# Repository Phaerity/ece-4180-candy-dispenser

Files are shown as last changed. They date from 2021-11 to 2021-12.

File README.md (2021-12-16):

# 🍭Automated Candy Dispenser🍬 (ECE 4180 Fall 2021)
Made by: Ikenna Nwokedi, Harneet Sethi, Felicia E, Anna Yue

## 🍫Project Description🍫
This device dispenses candy in a hands-free manner, similar to how hands-free soap dispensers work. The dispenser will use a lidar to detect motion and a DC motor to spin some blades that release candy. Inside the dispenser, there is a sonar to detect how much candy is left, and this information is displayed as a status bar using colored LEDs. The dispenser itself will sit on a robot chassis such that someone can drive it around using Bluetooth.  

See the automated candy dispenser in action! - https://youtu.be/Ra_htNfpPXM

## ⚡Parts List⚡
### Robot Chassis
Dual H-bridge (https://www.sparkfun.com/products/14450)  
2 DC motors (https://www.sparkfun.com/products/13302)  
Chassis parts from kit (Sparkfun Shadow Chassis https://www.sparkfun.com/products/13301)  
Bluetooth module (https://www.adafruit.com/product/2479)  
Adafruit app on Andriod/iOS (Bluefruit Connect)  
Battery pack (comes with Shadow Chassis)  
Mbed (https://www.sparkfun.com/products/9564)  
### Candy Dispenser
Lidar (https://www.adafruit.com/product/3317)  
Sonar (https://www.sparkfun.com/products/15569)  
LEDs (1 red, 1 green, 1 yellow) (https://www.sparkfun.com/products/12062)  
Transistor (https://www.sparkfun.com/products/12959)  
1 DC motor (same as above)  
Plywood/MDF (https://www.homedepot.com/p/1-4-in-x-2-ft-x-4-ft-Medium-Density-Fiberboard-1508104/202089069#overlay)  
2 Battery packs (same as above, or https://www.sparkfun.com/products/9835)  
Mbed (same as above)  
Speaker (https://www.sparkfun.com/products/11089)  
Class D amplifier (https://www.sparkfun.com/products/11044)  
RGB LED (https://www.sparkfun.com/products/10820)  
uLCD (https://www.sparkfun.com/products/11377)  

### Miscellaneous
Wires  
Candy (about the size of Hershey Kisses)  
Wood glue  
Super glue  
Electrical tape  
Masking tape  
AA batteries (or 5V wall plugs)

## 🛠️Tools Needed🛠️
Laser cutter  
3D Printer  
Drill  

# How It Works
## Sonar and Capacity Indicator LEDs
One component of the project is a sonar and led system that continuously measures the depth of candies in the dispenser and alerts the user to how full the box currently is by turning on separate LEDs.  

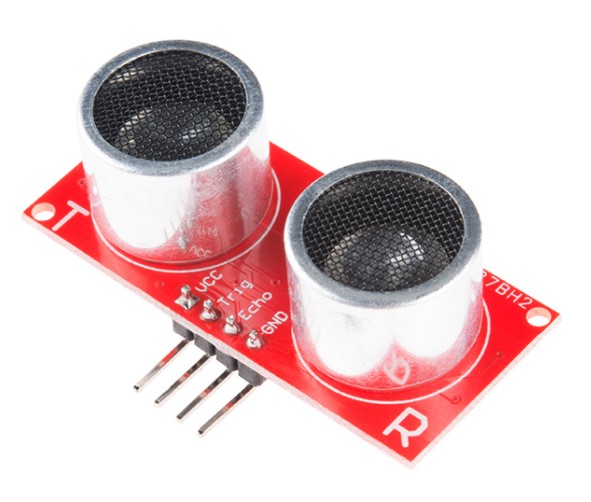
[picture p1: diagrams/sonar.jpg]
 
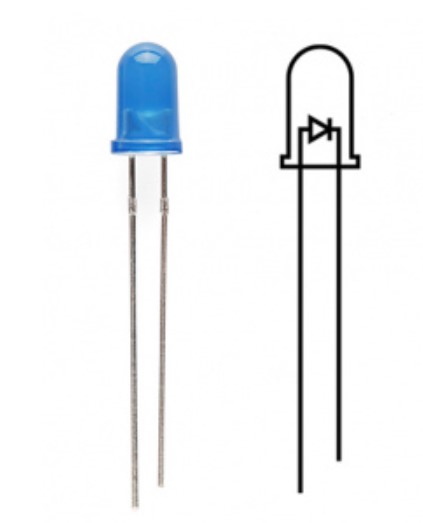
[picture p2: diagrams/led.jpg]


There are three LEDs: green to indicate a full box or a high level of candies, yellow to indicate a medium level of candies, and red to indicate a low level of candies that will need to be quickly replenished.

The sonar used is a HC-SR04 sonar module. It is mounted to the inside of the top of the box. The detection range is around3-400 cm with around a 15 degree beam width. Its transducers for transmitting and receiving signals are connected to the mbed microcontroller at pins 6 and 7. It uses its transducers to send out a signal and receive an echo back. The speed of sound and the time as returned by a timer interrupt for the delay transmission and reception are used to calculate the distance between the sonar and the candies closest to it.

Depending on the distance that the sonar measures, either one of the LEDs will be switched on while the others are turned off or all LEDs will be turned off and an error message will output through the COM port.  

## Lidar and DC Motor
Another component of the project is a lidar and DC motor system that performs the hand-motion detection and actual dispensing of the candy.  

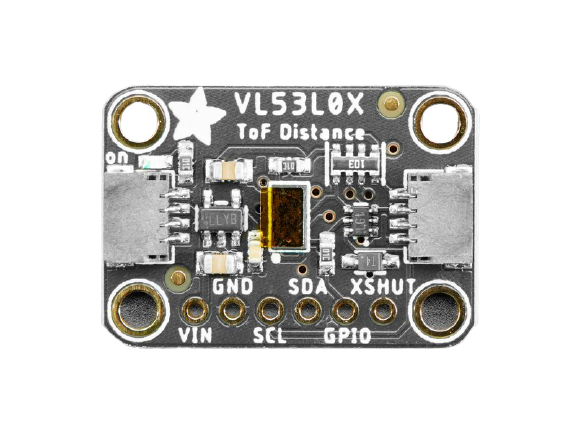
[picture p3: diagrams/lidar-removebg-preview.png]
 
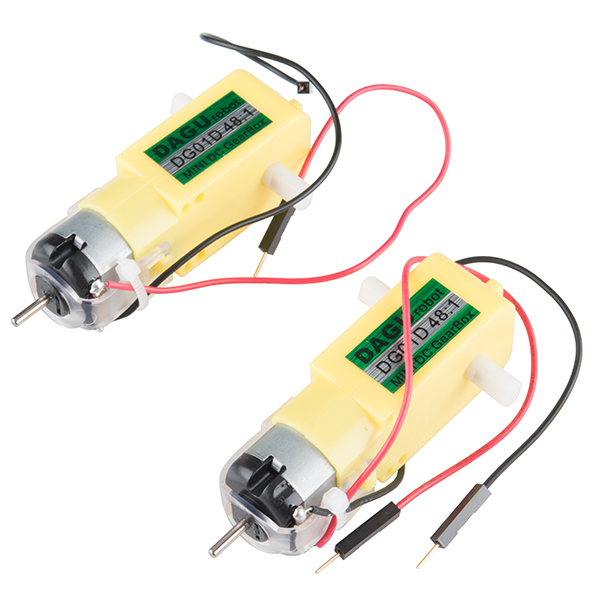
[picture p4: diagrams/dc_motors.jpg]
 

By reaching into the box with your hand open, the lidar is activated and the DC Motor will spin half a revolution, pushing out some candy with the attached 3D-printed blades.  

The lidar used is the VL53L0X module. It is able to detect distances from 30-1000 mm and works similarily to a sonar, except with light instead of ultrasonic waves and a smaller "cone" of detection.  

We specifically chose a lidar for this task due to the precision and reliability of the lidar measurements as well as its small size. Additionally, the lidar is situated pointing downwards so that it is always reading ~80 mm, so as soon as that reading drops to 65 mm it knows that some motion is being detected.  

The DC Motor is a standard motor that can be exchanged for a servo if desired. We primarily chose the DC Motor because the axle was easy to design a part to fit onto.  

## uLCD, Speaker, and RGB led
The last component of the candy dispenser itself includes the uLCD, speaker, and RGB led.  







Each of these devices alerts the user if their hand has been detected by changing state. At initialization and when no hand is detected, the uLCD provides instructions for how to use the automated dispenser, the RGB led is off, and the speaker is not playing any sounds. Upon a hand-motion detection, the lidar triggers the uLCD to display instructions on how to stop receiving candy, the RGB led is lit up white, and the speaker plays Ramblin' Wreck. This state is present until the hand is no longer detected.

The RGB led is placed on top of the dispenser for an easy visual indicator of whether a user's hand has been detected by the dispenser. The color of the RGB can be changed at any time in software, since the pin connections used support PWM. For the purposes of the prototype, white was used.

The speaker is attached to a breadboard which is mounted to the top of the inside of the dispenser. This design decision allows the dispenser to be more visually appealing, by concealing the speaker, but also provides an auditory indicator associated with the lidar detecting a hand motion. In some instances (depending on the sound/tone being played), the speaker needs to be driven for better audio quality. Therefore, this project includes a Class D Audio Amplifier (TPA2005D1) attached to the breadboard and wired to the speaker (pin connections included below). This approach uses PWM hardware which is more energy efficient than using analog. The SongPlayer header file is used in software, which means the song/sound and the volume can be easily changed/adjusted at anytime by modifying the appropriate parameters.

Lastly, the uLCD is mounted to the front of the dispenser so that the instructions can be viewed at all times by the users, even while the dispenser is moving on the chassis. The text, formatting, etc. on the uLCD can all be altered depending on the circumstance of when the dispenser is being used. The associated uLCD header file makes changing the settings of the uLCD very manageable. 

## Robot Chassis
The robot chassis consists of two DC motors, a dual TB6612FNG H-Bridge and an Adafruit Bluefruit LE UART Friend board.

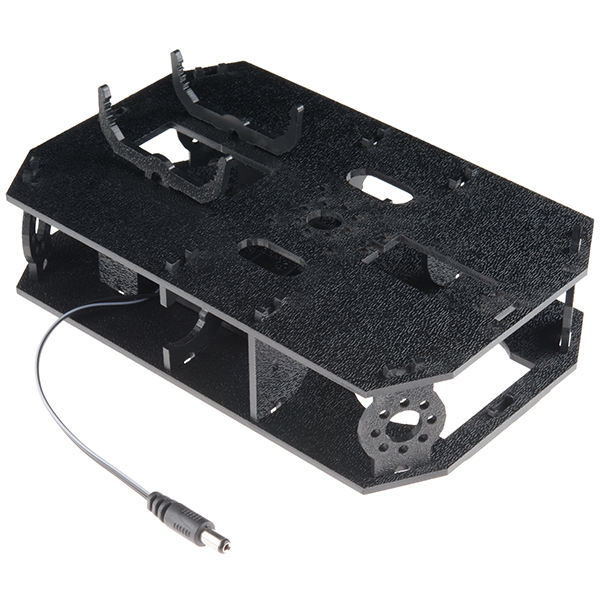
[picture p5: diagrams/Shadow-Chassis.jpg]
Shadow-Chassis

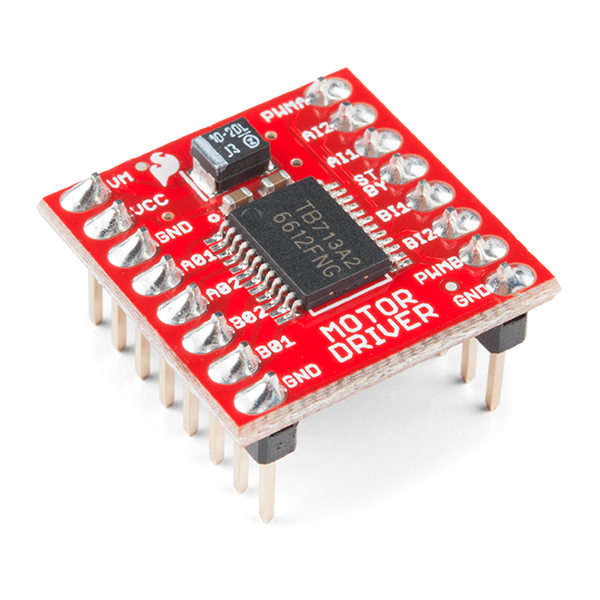
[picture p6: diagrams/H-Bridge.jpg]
H-Bridge

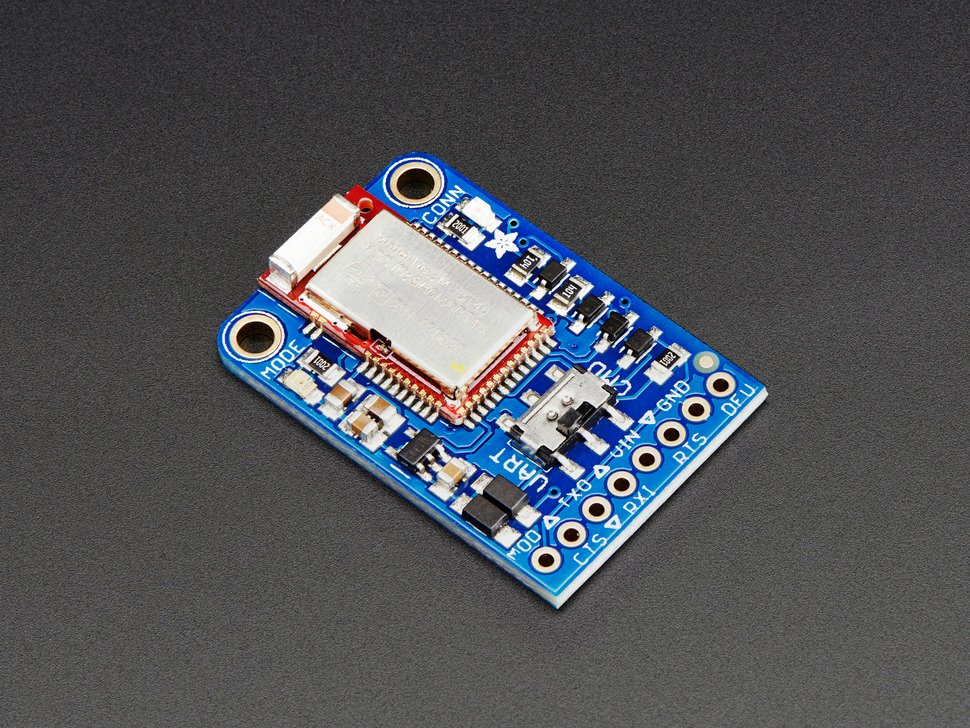
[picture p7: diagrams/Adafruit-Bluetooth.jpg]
Adafruit-Bluetooth


Using the Adafruit Bluefruit BLE app, buttons 1, 2, 3, and 4 are used to set the speed level of the wheels (on a scale from 0 to 1). While the up and down buttons move the motors forward and backward respectfully, the left and right buttons inverse the direction of both motors, resulting in a rotational movement around the chassis center. The motors gradually increase to their set speed for a duration of a second to keep the mbed from undervolting. This is done with a separate thread that starts once a directional button is pressed then terminates at the release of the button. Upon press of a button, an ASCII string is sent to the bluetooth board, which is then decoded in the mbed. More details can be found below.

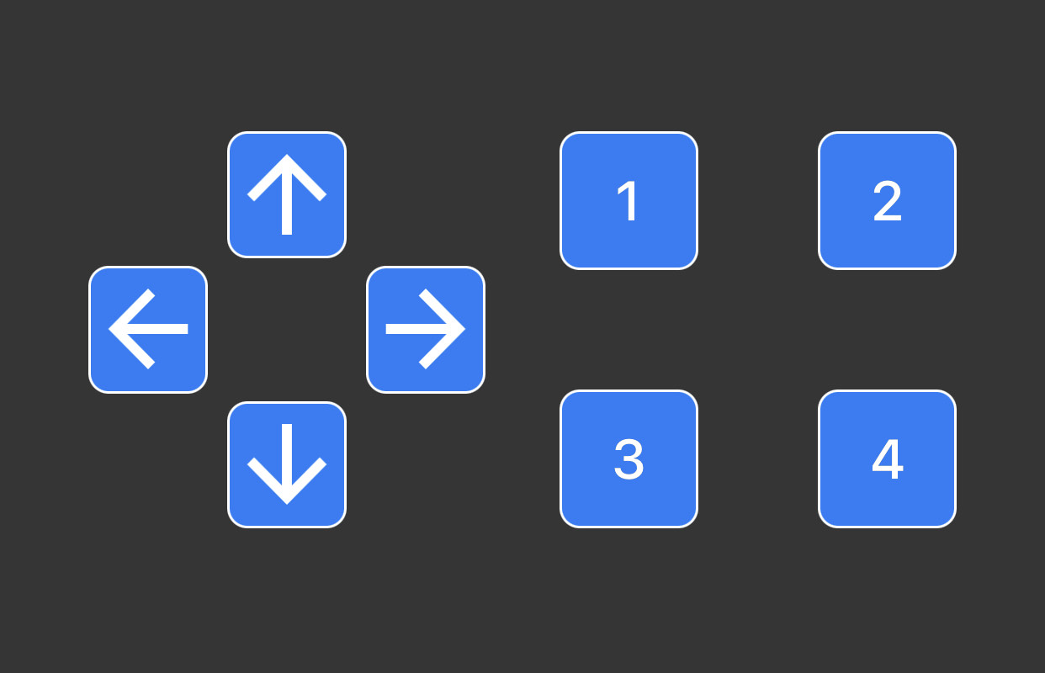
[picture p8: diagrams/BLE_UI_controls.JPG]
UI Controls


| GUI Touch Key  | ASCII String | Motor Function
|:---: |:---:|:---:|
| Button 1  | "!B11" | 0.25 of max speed |
| Button 2  | "!B21" | 0.50 of max speed |
| Button 3  | "!B31" | 0.75 of max speed |
| Button 4 | "!B41" | Max speed |
| Up Arrow  | "!B51" | Moves forward |
| Down Arrow  | "!B61" | Moves backwards |
| Left Arrow  | "!B71" | Turns left |
| Right Arrow  | "!B81" | Turns right |

# Instructions
## Cutting the Box
We started off by creating box using the website https://en.makercase.com/#/. The settings we used are as follows: Basic Box, Width 5 in., Height 8 in., Length 8 in., Outside dimensions, Material Thickness 1/4 in., Closed box, Finger joints sized 1.0915. These settings can be customized based on how big you want the dispenser to be and thickness of your wood. The box plans can be downloaded with labels disabled and separate panel layout, and these files can be used to laser cut the box at either the Hive or Invention Studio. The files we used (with Inkscape) are provided in the diagrams folder (box.svg).

> **Note:** For our project, we used 1/4" MDF to create the box, but we realize that lighter wood is preferable to reduce the weight of the dispenser. Therefore, you may want to consider using birch plywood or balsa wood.  

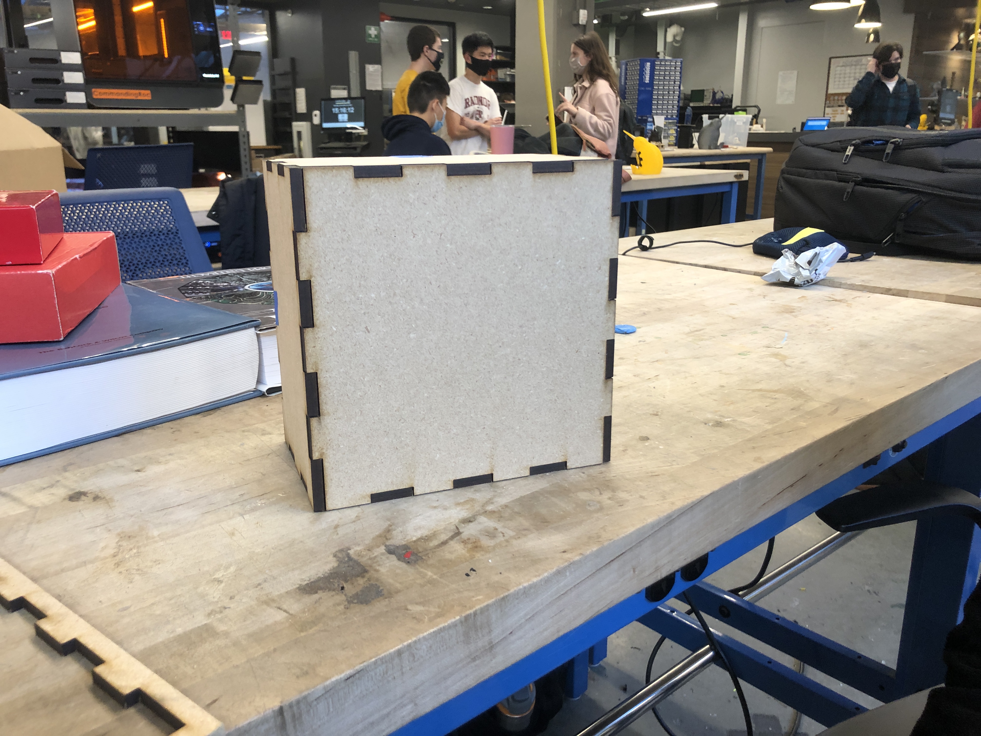
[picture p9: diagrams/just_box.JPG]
Laser Cut Box


Furthermore, the box must be modified so that the bottom panel becomes like a shelf (see picture). We cut rectangular holes into the sides of the box so that the shelf could "slide" in, but there are other ways to do it if preferable.  

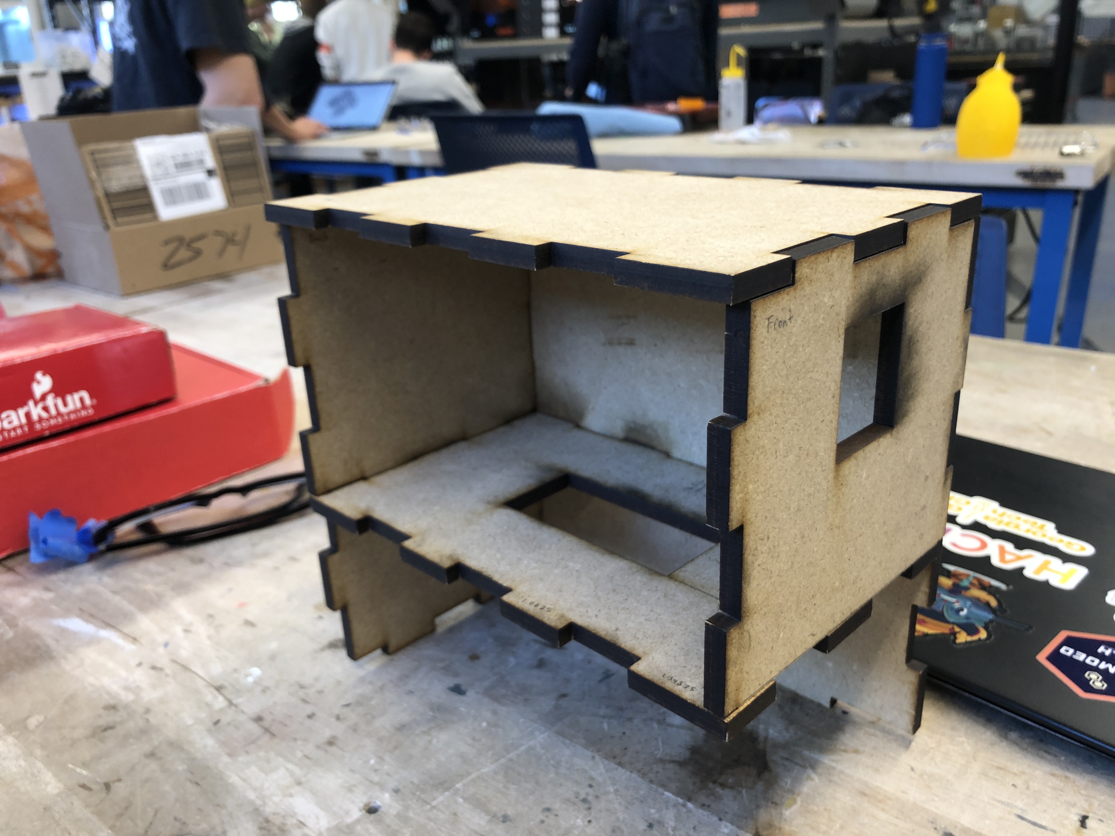
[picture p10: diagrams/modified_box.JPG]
Modified Box


An additional rectangular hole was cut on the back panel to facillitate wiring, but again this can be changed as you see fit.  
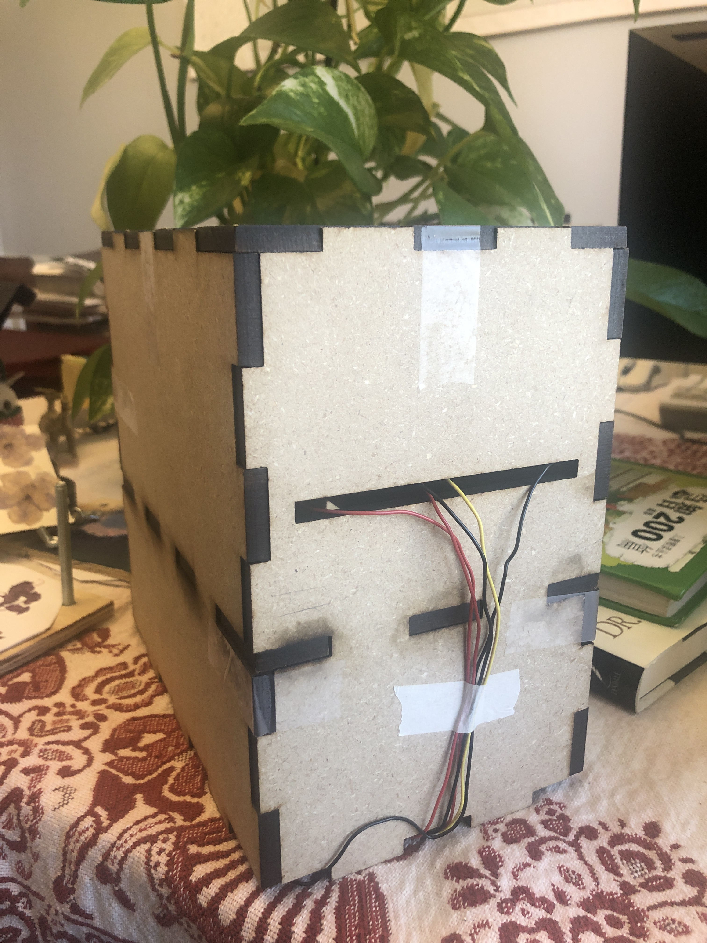
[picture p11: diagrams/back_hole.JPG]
Wire Hole Wiring hole
  

For the LED holes, we used a 7/32" drill bit and approximated the locations. The red, yellow, and green LEDs are on the front panel, and the RGB LED is on the top panel. For the uLCD hole, we cut a 32mm (width) by 38mm (length) rectangle on the front panel. For the windmill blade hole, we cut a 40mm (width) by 80mm (length) rectangle on the shelf panel.  

> **Note:** We originally proposed using an LED array to display the status for the amount of candy left, but we changed this to individual LEDs to avoid having to replace the parts at the end of the semester.

## The Blades
For the part that releases the candy (referred to as windmill blades), we created a CAD model to 3D print. We used Autodesk Inventor to draw the model before exporting it as an stl file and transferring it to 3D printer software. These files can be found in the diagrams folder (windmillv3.stl and windmillv3.ipt). Our windmill blades are made from PLA.  

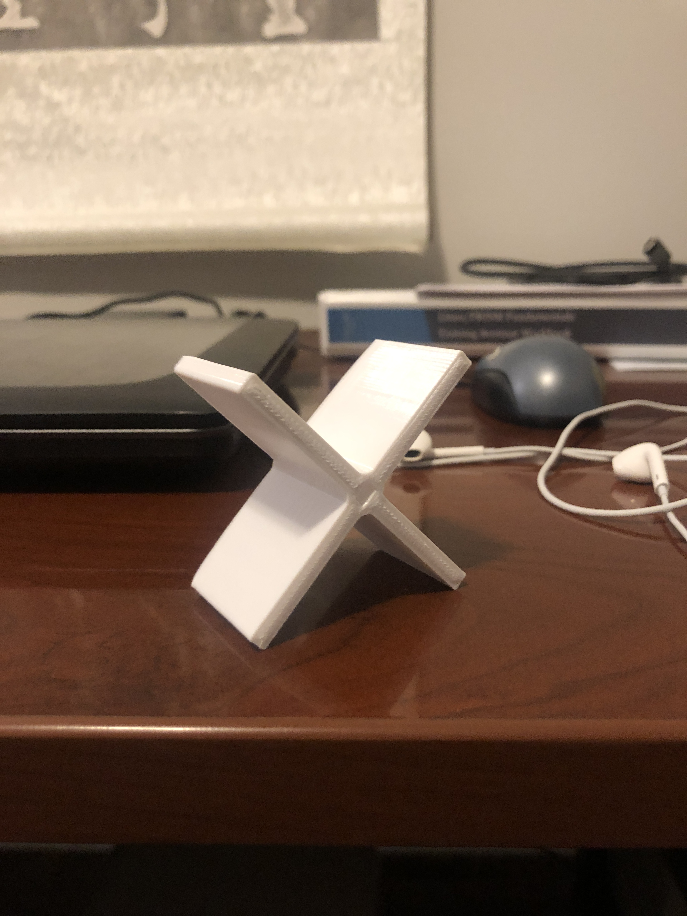
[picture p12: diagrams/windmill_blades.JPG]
Windmill Blades


## Assembling the Box
Once the box is cut with all the correct holes and the windmill blades are printed, we can start mounting components in the box. For the purposes of our prototype, components were either taped or glued down, but screws/standoffs are needed if a more permanent solution is desired.  

The uLCD can be first installed by pushing it into the rectangular hole in the front panel. There is a base on the uLCD that prevents it from going all the way through the hole. The windmill blades should snap onto the DC motor axle, and the motor should be positioned on the shelf panel so that the blades can spin freely through the rectangular hole in the shelf panel.  
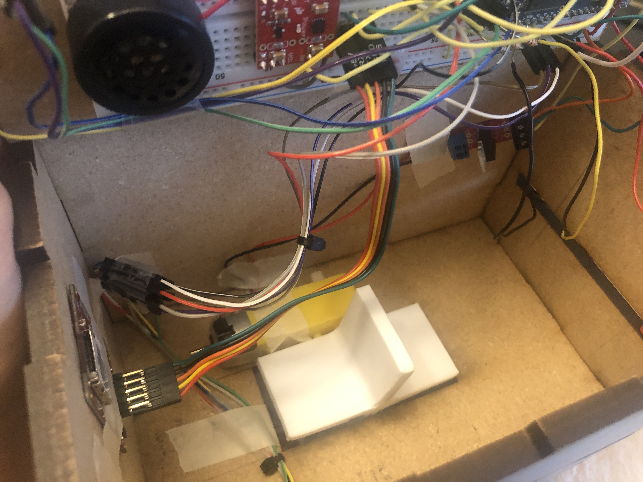
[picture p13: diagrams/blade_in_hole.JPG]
DC motor and blades DC motor and windmill blades
  
The sonar is attached to the underside of the top panel, such that it has a clear vision of the shelf panel without interference from the motor or blades.  
Under the lid Sonar, speaker, mbed under the lid  
The LEDs can be pushed through their respective holes and also have a base that prevent them from going all the way through the hole. The lidar is situated on a small breadboard that is attached to the underside of the shelf panel closest to the side where someone would stick their hand through.  

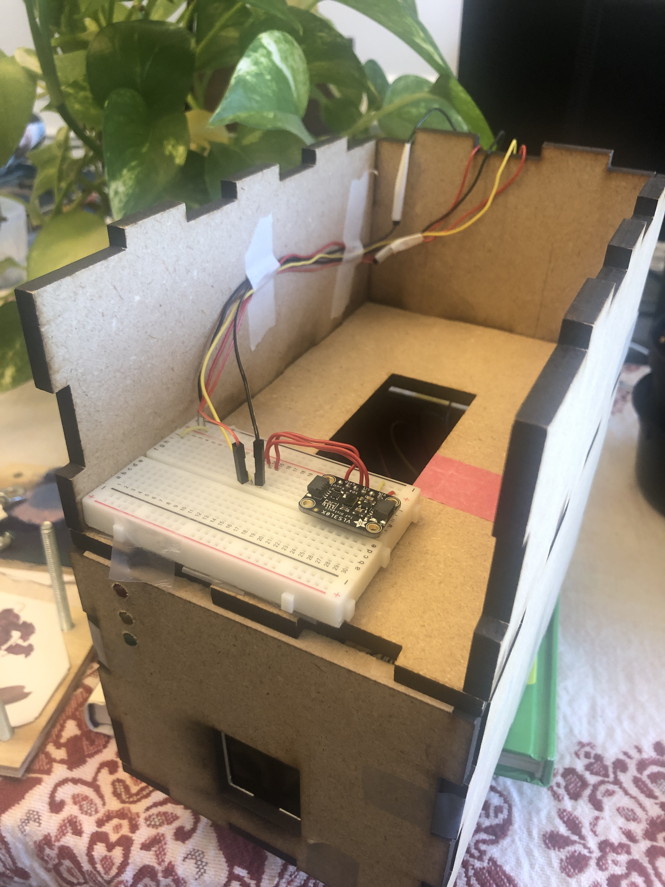
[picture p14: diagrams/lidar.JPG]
Lidar Lidar underneath
  

Once the components are in place, they can be wired following the schematics/tables below. 

Schematic 1

<table>
<tr><th> Sonar </th><th>LED </th></tr>
<tr><td>

| mbed | HC-SR04 |
| :----: |:----:|
| GND  | GND |
| VU (5V) | VCC |
| P6 | TRIG |
| P7 | ECHO |

</td><td>

| mbed | LEDs |
| :---: |:---:|
| GND  | RED(-), YELLOW (-), GREEN (-) |
| P12  | Red (+) |
| P13 | YELLOW (+) |
| P14 | GREEN (+)|
  
</td></tr> </table>

<table>
<tr><th> MOSFET </th><th> DC Motor </th></tr>
<tr><td>

| mbed | MOSFET (Transistor)|
| :---: |:---:|
| VU (5V) | GND (JP2-2 GND) |
| GND  | POWER (JP2-1 RAW) |
| P8  | CONTROL |

 </td><td>

| MOSFET (Transistor) | DC Motor |
| :---: |:---:|
| GND (JP1-2) | GND (-) |
| POWER (JP1-1) | POWER (+) |

</td></tr> </table>

<table>
<tr><th> Lidar </th><th> uLCD </th></tr>
<tr><td>

| mbed  | LIDAR (VL53L0X) |
| :---: |:---:|
| VOUT (3.3V) | VIN |
| VU (5V) | VCC |
| GND  | GND |
| P25  | SHDN |
| P27  | SCL |
| P28  | SDA |

</td><td>

| mbed  | uLCD HEADER | uLCD CABLE |
| :---: |:---:|:---:|
| GND  | GND | GND |
| VU (5V)  | 5V | 5V |
| P9 | RX | TX |
| P10 | TX | RX |
| P11 | RESET | RESET |

</td></tr> </table>

<table>
<tr><th> RGB LED connections </th><th>Speaker connections</th></tr>
<tr><td>

| mbed  | RGB LED |
| :---: |:---:|
| GND  | GND |
| P21  | RED |
| P22  | GREEN |
| P23  | BLUE |

</td><td>

| mbed  | Amp (TPA2005D1) | Speaker |
| :---: |:---:|:---:|
| GND  | PWR- (GND), IN- |
| VU (5V)  | PWR+ |
| P26  | IN+ |
| | OUT+ | + |
| | OUT- | - |

</td></tr> </table>

## The Chassis
The robot chassis can be assembled following the Sparkfun guide: https://learn.sparkfun.com/tutorials/assembly-guide-for-redbot-with-shadow-chassis. Bluetooth control is added using the Adafruit Bluefruit LE UART Friend board. The Adafruit board mini slide must be set to "UART" (not "CMD"). The "Adafruit Bluefruit BLE" app is used for the user interface and can be found on iOS and Andriod. Select "UART" mode on the phone window and connect to the board. A blue LED should turn on once connected.

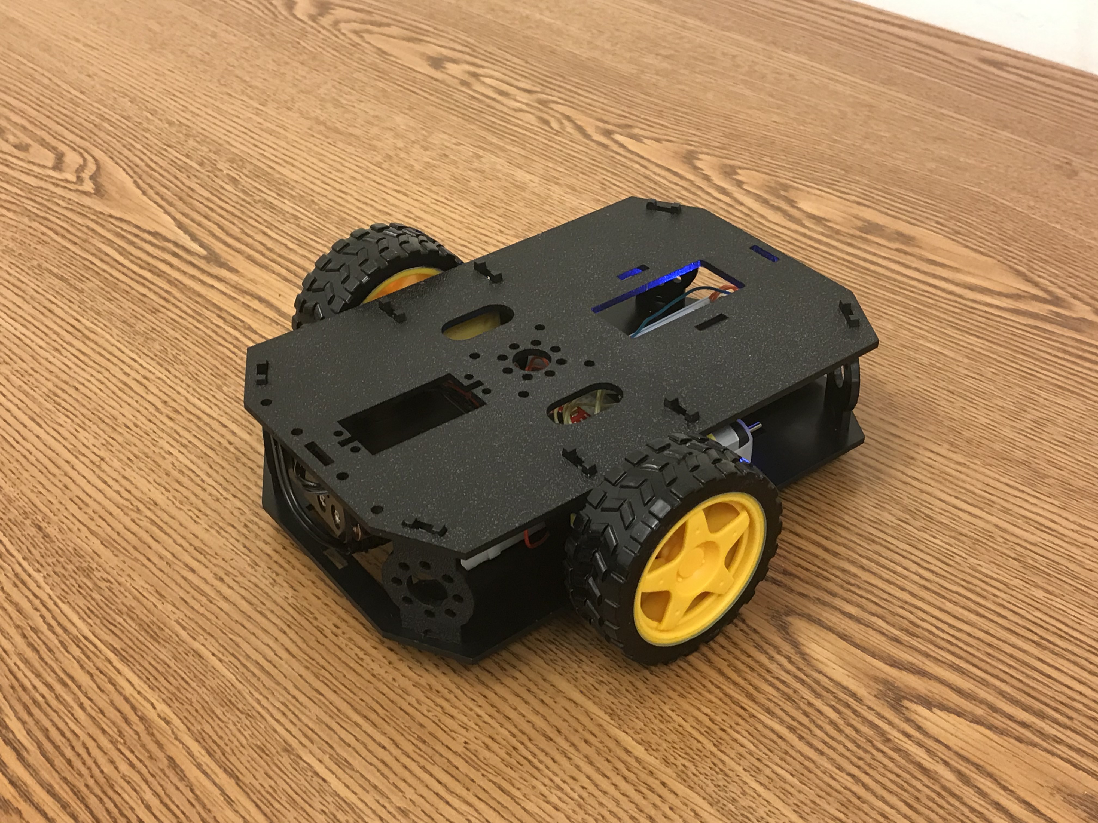
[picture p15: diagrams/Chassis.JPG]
Chassis

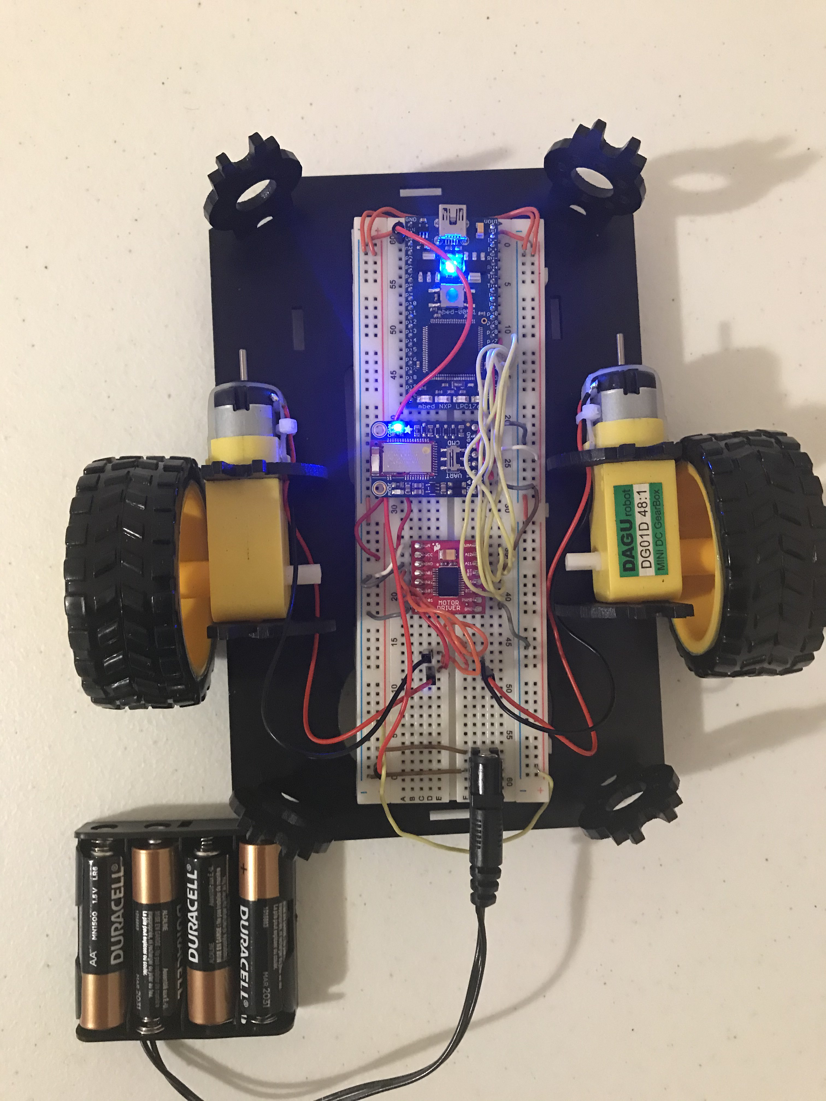
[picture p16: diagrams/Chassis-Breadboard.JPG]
Chassis Breadboard


A 6 V battery pack is used to power the two motors attached to the wheels. A dual H-bridge will regulate the speed and direction of the motor wheels. Both the breadboard implementation and the battery pack will fit into the robot chassis. The schematics/tables for the integration can be found below. 

Schematic 2

<table>
<tr><th> Bluetooth </th><th> H-Bridge </th><th> Motor </tr>
<tr><td>

| mbed | Adafruit BLE  |
| --- |:---:|
| VU (5V) | Vin (3.3-16V) |
| P27 (RX) | TXO |
| P28 (RX) | RXI |
| GND | GND |
| NC | RTS |

</td><td>

| mbed | H-Bridge |
| --- |:---:|
| P21 | PWMA |
| P22 | AIN1 |
| P23 | AIN2 |
| P24 | PWMB |
| P25 | BIN1 |
| P26 | BIN2 |
| VOUT | STBY |
| GND | GND |

</td><td>

| H-Bridge | Battery Pack | Left Motor | Right Motor |
|:---:|:---:|:---:|:---:|
|GND|GND  ||
|VM, VCC|5V|||
|A01||GND (BLACK)||
|A02||POWER (RED)||
|B01|||POWER(RED)|
|B02|||GND(BLACK)|

</td></tr> </table>

## Combining Everything
We found that the components for the dispenser drew too much current for one battery pack to handle, so we use two battery packs for the dispenser. Specifically, the DC motor is powered by one battery pack, and everything else is powered by the other battery pack. One battery pack sits on top of lid and one is located below shelf, sitting on top of chassis. 

The lidar, DC Motor, RBG LED, uLCD, speaker, sonar, and capacity LEDS are all controlled by a mbed microcontroller running multi-threaded RTOS code mounted on the inside of the top wooden pane. All devices except the DC motor and lidar are powered by one 5 V battery pack. The lidar uses 3.3 V output from the mbed micro controller and the DC motor has a separate battery pack for power, as mentioned before. Both battery packs are connected to two external power source connection jacks on a breadboard mounted on the back of the box. 

The dispenser box itself sits exactly on the top of the chassis. The chassis itself is controlled by a separate mbed microcontroller.

All code, for the dispenser devices as well as the robot chassis, can be found in the finalCode folder on this github page (chassis.cpp and the Motor folder are for the chassis mbed, main.cpp and everything else are for the dispenser mbed).   

## Conclusion

The completed candy dispenser robot is able to move forward, backward, left, and right as directed by the user's Bluefruit Connect application. The candy dispenser is able to drive up to a person and instruct them to "Place hand under dispenser to receive candy" in red text. Once the LIDAR sensor detect an object/the user's hand, it will trigger four events: a song will play from the speaker for as long as the user's hand is underneath the lidar, the uLCD's text will turn green to indicate the user's hand has been sensed, the RGB LED will flash on to indicate dispensing in progress, and the DC motor will turn to release a candy. The entire time, the sonar will be constantly measuring the depth of candy in the box; turning on the green, yellow, and red LEDs respectively when the candy volume is high, medium, or low.

giphy

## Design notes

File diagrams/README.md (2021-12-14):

# Diagrams/Pictures

🖼️🖼️🖼️

Schematic 1

Schematic 2

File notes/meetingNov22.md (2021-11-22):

# In-Person Meeting 11/22/21
Members present: Harneet, Felicia, Ikenna, Anna

# Notes
## Diagramming robot
We drew out how the robot looks in full, including all parts and where they will be in relation to the robot:
Whiteboard drawings  
Felicia diagrammed a 3D version of the robot in Paint 3D

### There will be 3 "levels" built out of wood:
1. Bottom level houses the mbed, motors, and bluetooth for the robot chassis
2. Middle level is open for a hand to insert into - like a square with 3 sides
3. Top level is the actual dispenser, with the candy
### Changing LED array to individual for fullness status
To avoid having to take it apart at the end of the semester - **add to the report** since changed from the original design
### Structure to dispense the candy is similar to a windmill, turns 90 degrees to dispense
There will be a rectangular hole at the bottom of the actual dispenser
### Inside the actual dispenser, we can install slanted boards to help with candy not getting stuck at the corners (OPTIONAL)
### The mbed and speaker for the actual dispenser will be mounted on the back, exposed
### The sonar will be on the ceiling of the dispenser
### The lid will be separate from the box
Will need to be detachable - hinge, velcro, tape, etc.

# TODO
Port to github.com, github.gatech.edu will require logon for the grader  
Finish wood stuff by Dec. 3 - Invention Studio will close by then so no laser cutter

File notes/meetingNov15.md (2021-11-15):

# 11/15/21 Virtual Meeting

Members present: Ikenna, Felicia, Harneet, Anna

## Splitting project into 4 parts
1. Motion sensing + opening/closing latch (lidar + servo) - Anna
    - Ikenna has motion sensing code for arduino from previous project
2. Robot chassis + bluetooth (bluefruit app) to drive + power (on its own mbed) - Ikenna
3. Sonar + LED array (status for fullness) + building the box - Felicia
4. LEDs (+ LCD maybe) for decoration (open for interpretation) + speaker/sound + power (battery pack) - Harneet

All help with robot if needed  
Next meeting draw out how it all looks together (esp. box)

## Requirements:
Documentation on the project web page must include team member names, a parts list, schematic, source code, photos, and videos.  

The web page should explain the project idea, provide instructions, code, and hardware setups so that anyone could recreate your project along with photos and videos along with team member names. It might make sense to have a longer video on the web page 

### Ask Dr. Hamblen:
Show what we have, see if it's what he meant (Github documentation)  
Is github.gatech.edu okay?  
Lab still open?

### Other notes:
Maybe don't use LED array because will have to return it - uLCD instead of this? ask Oscar or Maddie

## Schedule:
Nov. 22 - meeting to draw out how it all looks/interacts together (Hive 12:30, whiteboard)  
Nov. 22-30 - Work on individual parts, help others if needed  
Nov. 29 - class time to make sure all individual parts are working  
Dec. 1 & 6 - class time to put everything together  
Dec. 1-10 - Integration  
Dec. 11-14 - Finalize documentation and presentation  
Dec. 15 - presentation day  
  
How to format this page: https://docs.github.com/en/github/writing-on-github/getting-started-with-writing-and-formatting-on-github/basic-writing-and-formatting-syntax

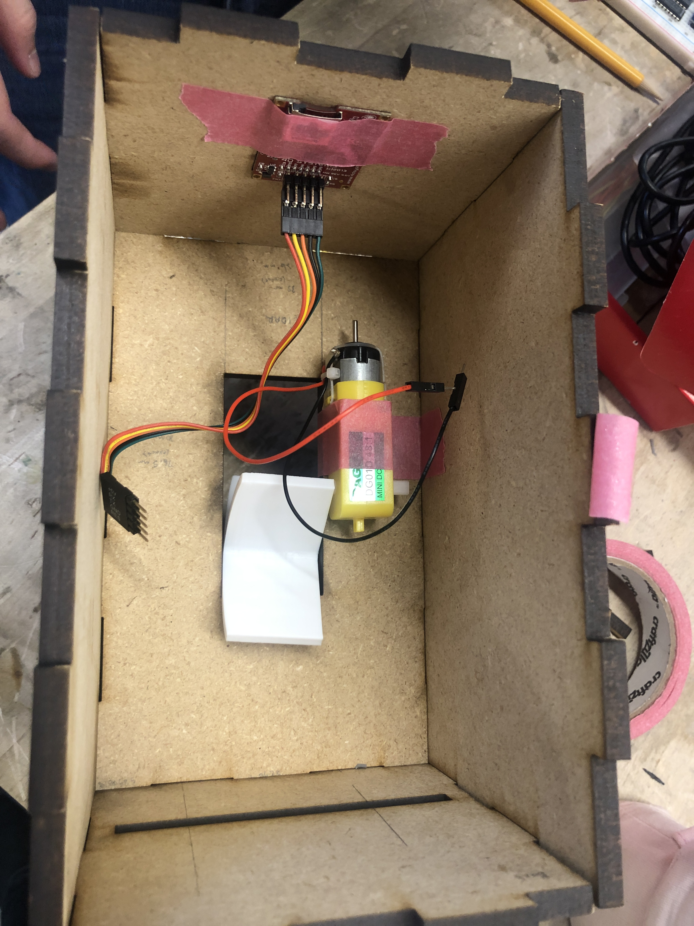
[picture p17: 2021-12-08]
diagrams/mount_lcd.JPG

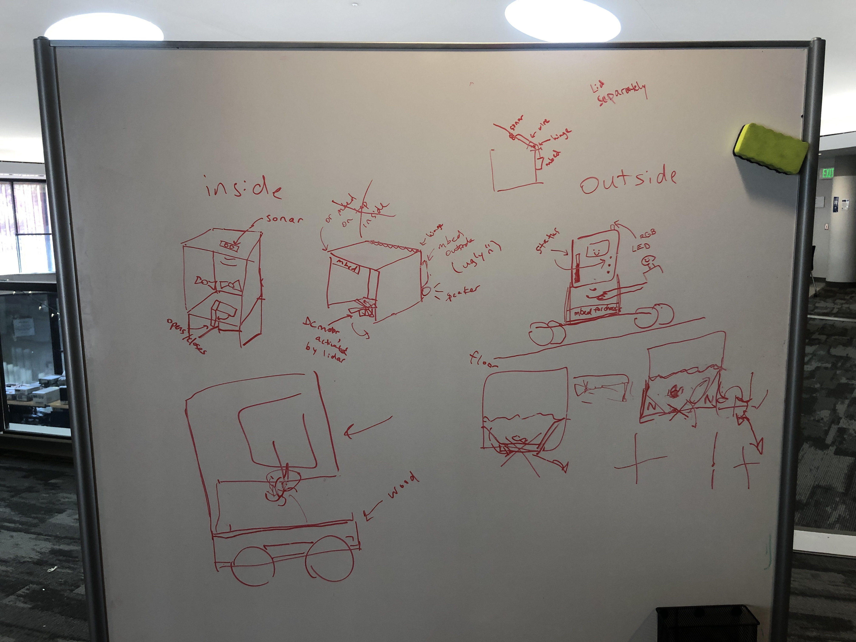
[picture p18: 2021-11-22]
diagrams/whiteboardNotes.JPG

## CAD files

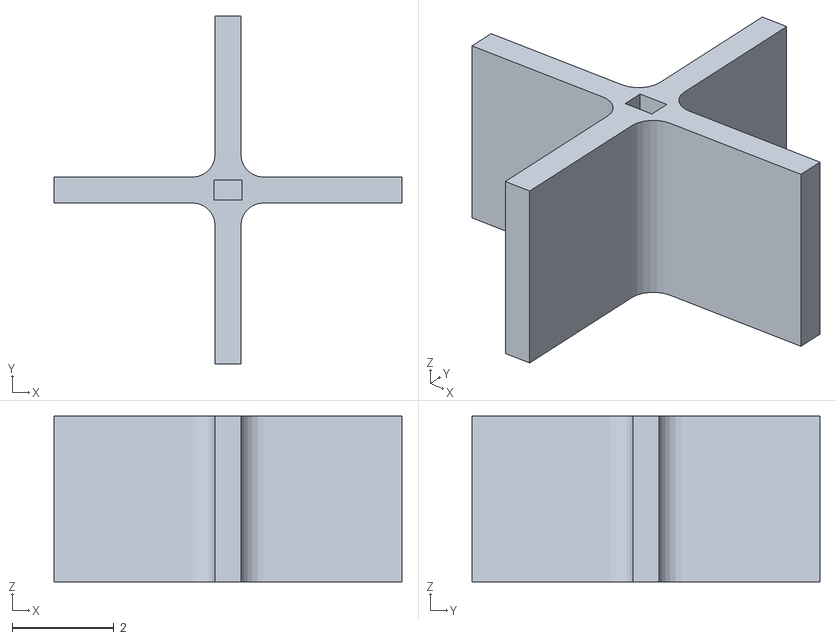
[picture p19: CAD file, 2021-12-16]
diagrams/windmillv3.stl
6.83 x 6.83 x 3.25

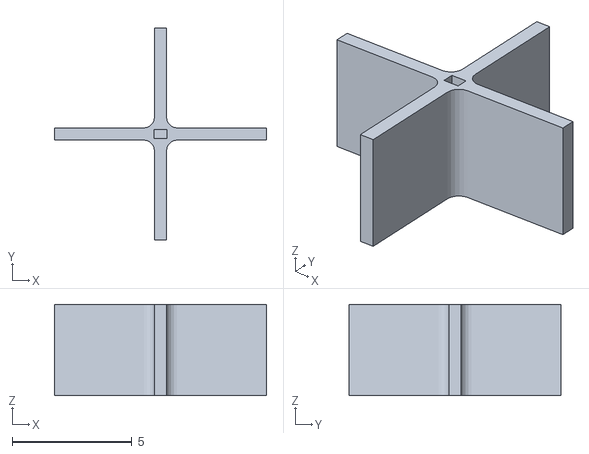
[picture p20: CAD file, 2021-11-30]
diagrams/windmillv2.stl
8.87 x 8.87 x 3.81

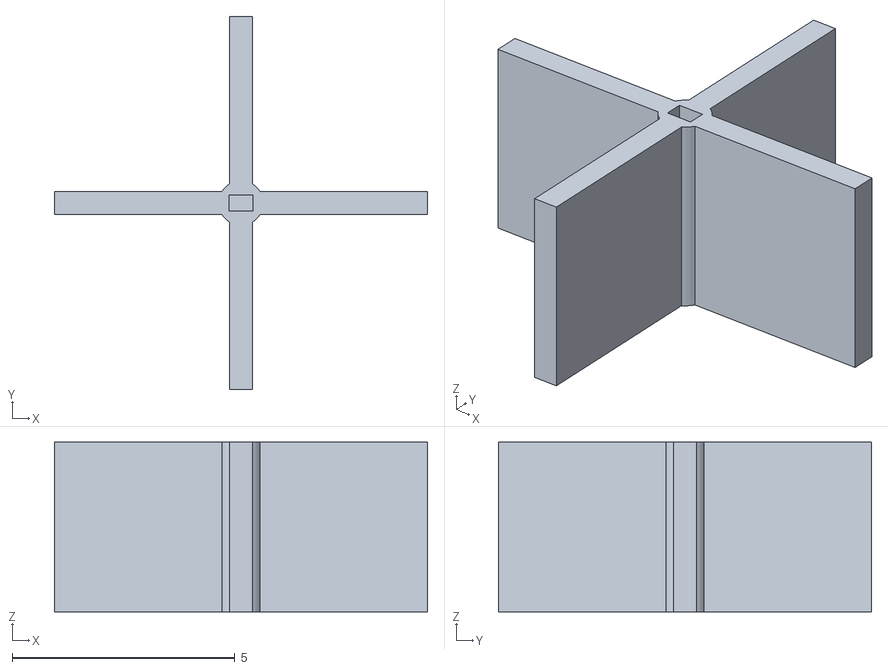
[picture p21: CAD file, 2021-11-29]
diagrams/windmill.stl
8.37 x 8.37 x 3.81

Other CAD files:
diagrams/windmill.ipt
diagrams/windmillv2.ipt
diagrams/windmillv3.ipt

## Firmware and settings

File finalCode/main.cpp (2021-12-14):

/*
 * Main code for automated candy dispenser.
 *
 * Adapted from RTOS, lidar, and sonar hello world code.
 */

#include "mbed.h"
#include "rtos.h"
#include "XNucleo53L0A1.h"
#include <stdio.h>
#include "uLCD_4DGL.h"
#include "SongPlayer.h"

Serial pc(USBTX,USBRX);
uLCD_4DGL uLCD(p9,p10,p11); // serial tx, serial rx, reset pin;

//Set up notes and durations for sample song to play
// A 0.0 duration note at end terminates song play
float note[18]= {1568.0,1396.9,1244.5,1244.5,1396.9,1568.0,1568.0,1568.0,1396.9,
                 1244.5,1396.9,1568.0,1396.9,1244.5,1174.7,1244.5,1244.5, 0.0
                };
float duration[18]= {0.48,0.24,0.72,0.48,0.24,0.48,0.24,0.24,0.24,
                     0.24,0.24,0.24,0.24,0.48,0.24,0.48,0.48, 0.0
                    };

// For the sonar
DigitalOut trigger(p6);
DigitalIn  echo(p7);

float distance = 0;
float correction = 0;
Timer sonar;
DigitalOut red(p12);
DigitalOut yellow(p13);
DigitalOut green(p14);

// For the lidar
DigitalOut RGBred(p21);
DigitalOut RGBgreen(p22);
DigitalOut RGBblue(p23);

SongPlayer mySpeaker(p26);
volatile bool changed = false;

DigitalOut shdn(p25);
 
DigitalOut myled(LED1); // comment out later
PwmOut Ctrl(p24);
// This VL53L0X board test application performs a range measurement in polling mode
// Use 3.3(Vout) for Vin, p28 for SDA, p27 for SCL, P26 for shdn on mbed LPC1768

//I2C sensor pins
#define VL53L0_I2C_SDA   p28
#define VL53L0_I2C_SCL   p27

static XNucleo53L0A1 *board=NULL;

// Callback routine is interrupt activated by lidar
/*void pb_hit_callback (void) {

    //mySpeaker = 0.5;
    mySpeaker.PlaySong(note, duration, 0.1);
    RGBred = 1;
    RGBgreen = 1;
    RGBblue = 1;
    //Put uLCD stuff here
    uLCD.cls();
    uLCD.color(GREEN);
    //uLCD.locate(2,1);
    uLCD.printf("Remove hand to stop receiving candy\n");
    changed = true;
}*/

// Thread 1
// sonar detection
void thread1(void const *args)
{
    sonar.reset();
    // measure actual software polling timer delays
    // delay used later in time correction
    // start timer
    sonar.start();
    // min software polling delay to read echo pin
    while (echo==2) {};
    // stop timer
    sonar.stop();
    // read timer
    correction = sonar.read_us();
    pc.printf("Approximate software overhead timer delay is %f uS\n\r", correction);

    //Loop to read Sonar distance values, scale, and print
    while(1) {
    // trigger sonar to send a ping
        trigger = 1;
        sonar.reset();
        wait_us(5.0);
        trigger = 0;
    //wait for echo high
        while (echo==0) {};
    //echo high, so start timer
        sonar.start();
    //wait for echo low
        while (echo==1) {};
    //stop timer and read value
        sonar.stop();
    //subtract software overhead timer delay and scale to cm
        //printf("The time taken was %d seconds\n", sonar.read_us());
        ::distance = (sonar.read_us()-correction)/58.0;
        //pc.printf(" %f cm \n\r", ::distance);
        if (::distance <= 6.53) {
            green = 1;
            yellow = 0;
            red = 0;
            //pc.printf("GREEN \n\r");
        } else if ((::distance > 6.53) && (::distance <= 8.167)) {
            green = 0;
            yellow = 1;
            red = 0;
            //pc.printf("YELLOW \n\r");
        } else if ((::distance > 8.167) && (::distance <= 9.8)) {
            green = 0;
            yellow = 0;
            red = 1;
            //pc.printf("RED \n\r");
        } else if (::distance > 9.8) {
            green = 0;
            yellow = 0;
            red = 1;
            //pc.printf("ERROR: %f cm is larger than the box \n\r", ::distance);
        }
            
    //wait so that any echo(s) return before sending another ping
        Thread::wait(50);
    }
}

int main()
{
    int status;
    uint32_t distance;
    DevI2C *device_i2c = new DevI2C(VL53L0_I2C_SDA, VL53L0_I2C_SCL);
    /* creates the 53L0A1 expansion board singleton obj */
    board = XNucleo53L0A1::instance(device_i2c, A2, D8, D2);
    shdn = 0; //must reset sensor for an mbed reset to work
    wait(0.1);
    shdn = 1;
    wait(0.1);
    /* init the 53L0A1 board with default values */
    status = board->init_board();
    while (status) {
        pc.printf("Failed to init board! \r\n");
        status = board->init_board();
    }
    
    // Setup Interrupt callback function for a pb hit
    //pb.attach_deasserted(&pb_hit_callback);
    pc.printf("Initialized lidar\r\n");
    
    // Init ulcd
    uLCD.cls();
    uLCD.baudrate(3000000); //jack up baud rate to max
    uLCD.text_height(2);
    uLCD.text_width(2);
    uLCD.color(RED);
    uLCD.printf("Place hand under dispenser to receive candy!\n");
    changed = false;
    
    pc.printf("initizlized ulcd\r\n");
    
    // start threads
    Thread t1(thread1); //start thread1
    
    pc.printf("Starting main loop\r\n");
    //loop taking and printing distance
    while (1) {
        status = board->sensor_centre->get_distance(&distance);
        if (status == VL53L0X_ERROR_NONE) {
            //pc.printf("D=%ld mm\r\n", distance);
            RGBred = 0;
            RGBgreen = 0;
            RGBblue = 0;
            mySpeaker.PlaySong(note, duration, 0.0);
            if (changed) {
                uLCD.cls();
                uLCD.color(RED);
                uLCD.printf("Place hand under dispenser to receive candy!\n");
                changed = false;
            }
            
            if (distance < 70) {
                Ctrl = 0;
                for (int i = 0; i < 10; i++) {
                    Ctrl = Ctrl + 0.1;    
                }
                Thread::wait(80);
                for (int i = 0; i < 10; i++) {
                    Ctrl = Ctrl - 0.1;    
                }
                
                mySpeaker.PlaySong(note, duration, 0.01);
                RGBred = 1;
                RGBgreen = 1;
                RGBblue = 1;
                //Put uLCD stuff here
                uLCD.cls();
                uLCD.color(GREEN);
                uLCD.printf("Remove hand to stop receiving candy\n");
                changed = true;
                
                while (distance < 70) {
                    status = board->sensor_centre->get_distance(&distance);
                    Thread::wait(10);
                }
                //Thread::wait(4500);
            }
        }
        Thread::wait(10);
    }
}

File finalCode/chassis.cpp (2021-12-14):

#include "mbed.h"
#include "Motor.h"
#include "rtos.h"

Motor DC_Motor_Left(p21, p22, p23);
Motor DC_Motor_Right(p24, p25, p26);
Serial Blue(p28, p27);
Serial pc(USBTX, USBRX);
Thread MotorThread;

#define SPEED1 0.25f
#define SPEED2 0.50f
#define SPEED3 0.75f
#define SPEED4 1.0f

float curr_speed = SPEED1;
float left_speed = 0.0f;
float right_speed = 0.0f;
float direction = 1.0f;

void startMotors() {
    float inten = 0.0f;
    while (inten < 1.0f) {
        DC_Motor_Left.speed(inten * direction * left_speed);
        DC_Motor_Right.speed(inten * direction * right_speed);
        inten+=0.10f;
        Thread::wait(200);
    }
}

int main() {
    char bnum = 0;
    while(1) {
        if (Blue.getc()=='!') {
            if (Blue.getc()=='B') {
                bnum = Blue.getc();
                if (Blue.getc() == '1') {
                    switch(bnum) {
                        case '1':
                            curr_speed = SPEED1;
                            break;
                        case '2':
                            curr_speed = SPEED2;
                            break;
                        case '3':
                            curr_speed = SPEED3;
                            break;
                        case '4':
                            curr_speed = SPEED4;
                            break;
                        case '5':
                            left_speed = curr_speed;
                            right_speed = curr_speed;
                            direction = 1.0f;
                            printf("UP\n");
                            break;
                        case '6':
                            left_speed = curr_speed;
                            right_speed = curr_speed;
                            direction = -1.0f;
                            printf("DOWN\n");
                            break;
                        case '7':
                            left_speed = curr_speed * -1.0f;
                            right_speed = curr_speed;
                            printf("LEFT\n");
                            break;
                        case '8':
                            left_speed = curr_speed;
                            right_speed = curr_speed * -1.0f;
                            printf("RIGHT\n");
                            break;
                    }
                    if (bnum == '5' || bnum == '6' || bnum == '7'|| bnum == '8') {
                        MotorThread.start(startMotors);
                    }
                } else {
                    MotorThread.terminate();
                    DC_Motor_Left.speed(0);
                    DC_Motor_Right.speed(0);
                }
            }
        }
    }
}

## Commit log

2021-11-29 Added 3D printed windmill part (version 1)
2021-11-29 Added files needed to print windmill blades
    [windmill.ipt, windmill.stl]
2021-11-30 Updated windmill dimensions
    [windmillv2.ipt, windmillv2.stl]
2021-11-30 Added files for lidar sample code
2021-12-08 Uploaded speaker, uLCD, and rgb LED code
2021-12-11 Update README.md
    Added short description of sonar and LEDs
2021-12-11 Updated windmill blade length
    [windmillv3.ipt, windmillv3.stl]
2021-12-11 Update windmill blades length
    [windmillv3.ipt, windmillv3.stl]
2021-12-11 Update windmill files
    [windmillv3.ipt, windmillv3.stl]
2021-12-11 Updated windmill files
    [windmillv3.ipt, windmillv3.stl]
2021-12-14 Added sonar code
2021-12-14 Added pics of where to mount stuff
